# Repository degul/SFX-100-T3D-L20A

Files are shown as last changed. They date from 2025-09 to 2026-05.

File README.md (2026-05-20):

# SimFeedback-T3D-L20A
SFX-100 AC Servo Motor 80AST-A1C02430

카카오톡 오픈 톡방 - https://open.kakao.com/o/gSO9CL0h

3d view - https://a360.co/4tRbJ65

## Servo Motor wiring diagram

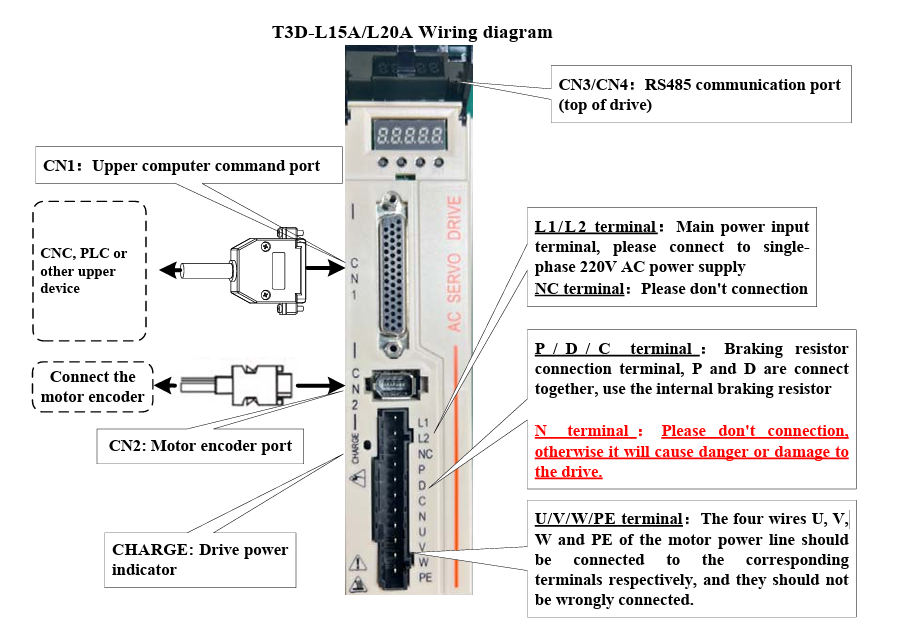
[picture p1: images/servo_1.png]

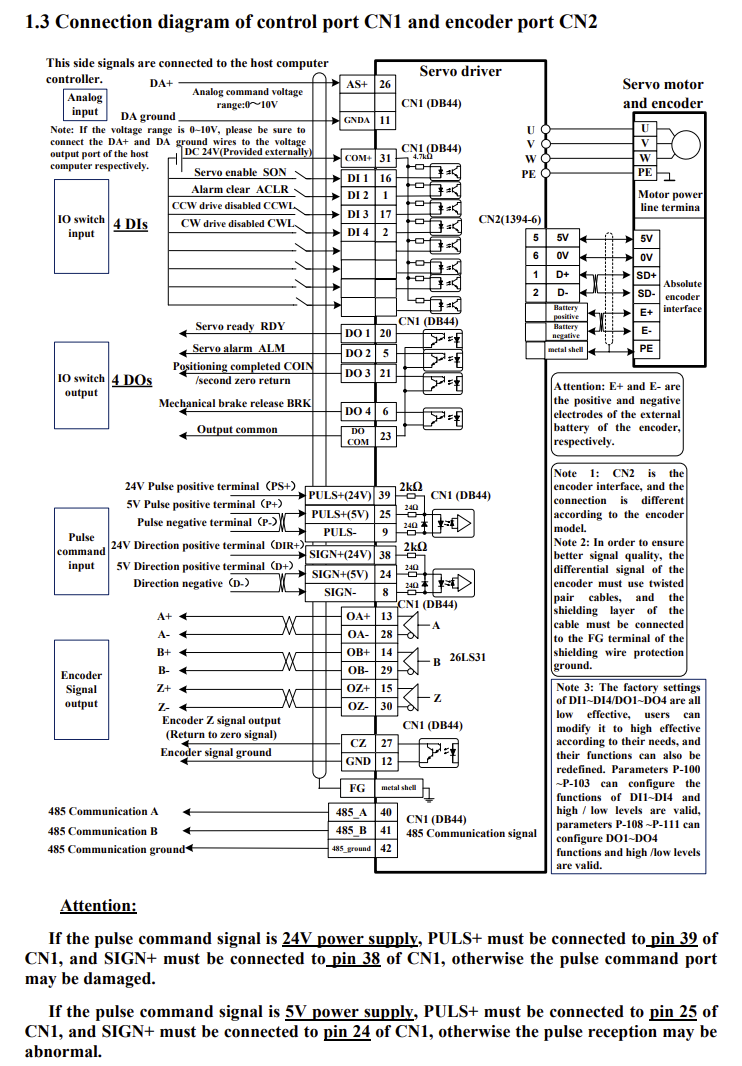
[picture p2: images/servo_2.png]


` L1 / L2 = main power input terminal 220v  `<br>
` U / V / W / PE = motor power cable  `<br>

## SimFeedback + Servo 80AST Pins

### 아두이노 핀 정보

| Pin | Motor 1 | Motor 2 | Motor 3 | Motor 4 | DB25 PIN |
|---|---|---|---|---|---|
| STEP  | 8 | 9 | 10 | 11 | 3 |
| DIR | 4 | 5 | 6 | 7 | 4 |
| ENA | A0 | A1 | A2 | A3 | 6 |
| 5V | 5V | 5V | 5V | 5V | 9 |
| GND | GND | GND | GND | GND | 5, 10, 14 |

### DB25 터미널에 모터드라이브 배선 연결 정보

| DB25 Pin | Label |
|---|---|
| 3 | **P+** |
| 4 | **D+** |
| 6 | **SON** |
| 9 | **24V** |
| 5,10,14  | **P- / D- / 0V** |
---

## 모터드라이브 파라미터

` P-006 ; 25 `<br>
` P-007 ; 30 `<br>
` P-019 ; 60 `<br>
` P-021 ; 20 `<br>
` P-029 ; 16 = 100mm stroke limit `<br>
` P-040 ; 30 `<br>
` P-098 ; 1 (Force Enable)`<br>

### $\color{red}{\textbf{E-set -> done}}$  (값 설정후 저장 및 재시작)
---

<br>
<br>

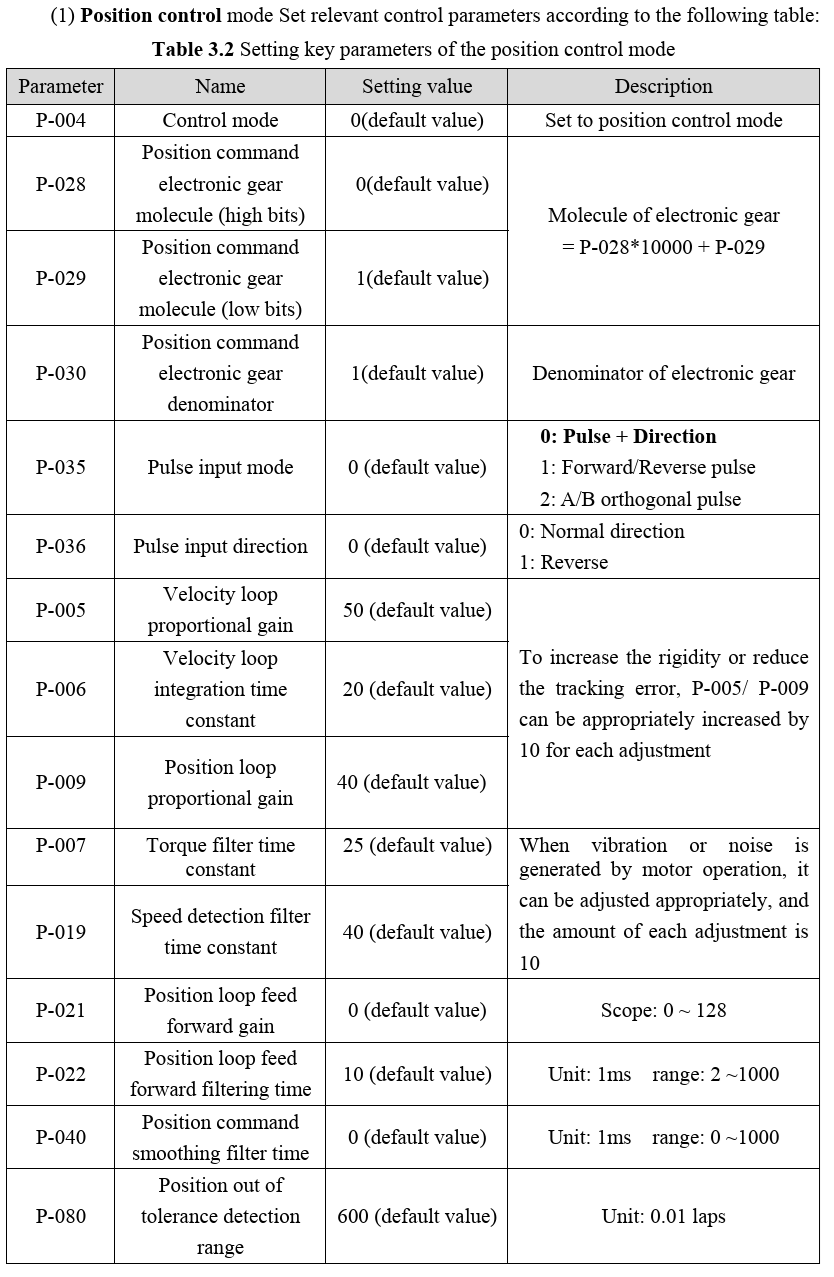
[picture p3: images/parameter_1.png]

<!-- <img src="https://github.com/degul/SimFeedback-T3D-L20A/raw/main/images/parameter_2.png" alt="" width="600"> -->

## SFX-100 

3d view - https://a360.co/4tRbJ65

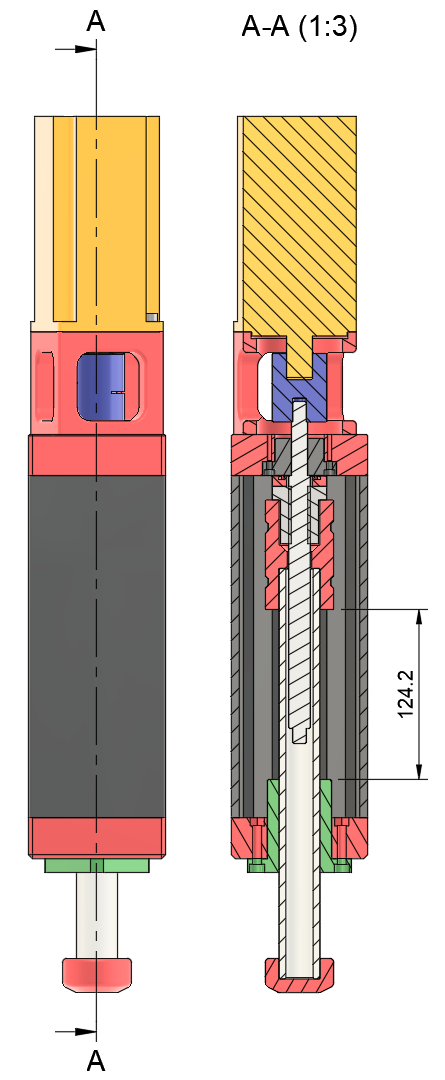
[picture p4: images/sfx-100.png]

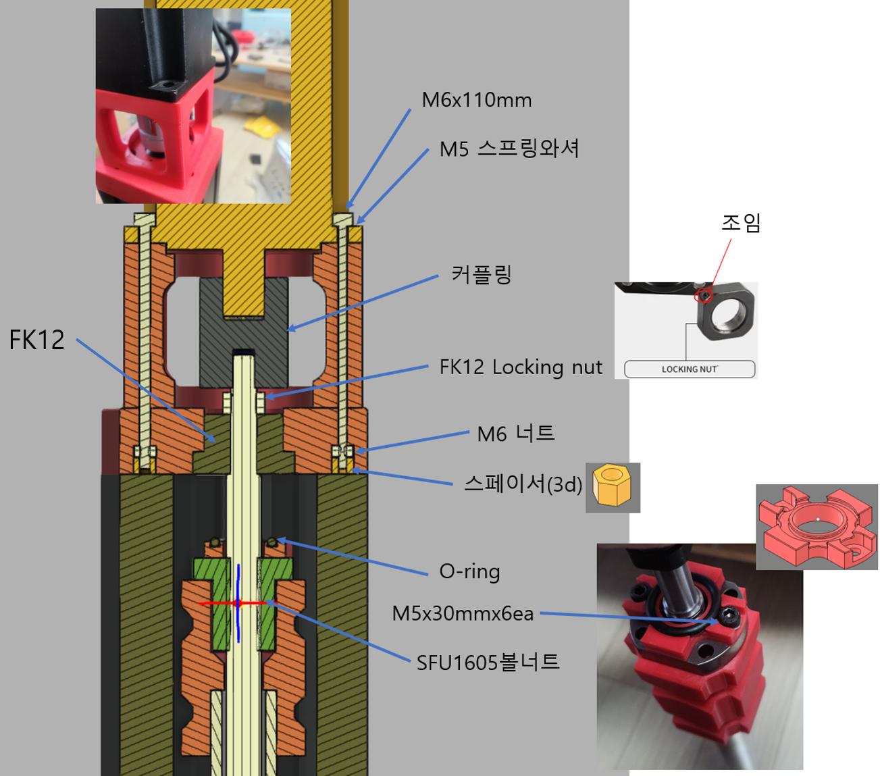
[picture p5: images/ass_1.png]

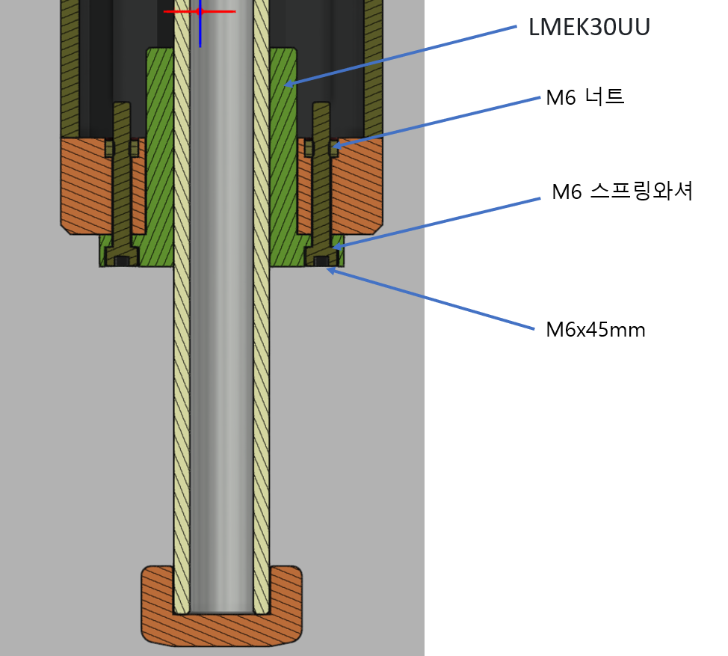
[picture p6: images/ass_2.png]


## Assembly parts

| Part | Type | EA | Link | 
| --- | --- | --- | --- |
| Servo Motor | HLTNC T3D-L20A-RABN 750W 2.4N | 4 | https://www.aliexpress.com/item/1005004869497167.html |
| Coupling | 40X50-10X19 | 4 | https://www.aliexpress.com/item/33014472676.html |
| Rubber Ring | OD30mm CS4mm | 1 (50pcs) | https://www.aliexpress.com/item/1005008292700053.html |
| FK12 |  | 4 | https://www.aliexpress.com/item/32717973925.html |
| SFU 1605 | 250mm, SFU1605(metal nut, 메탈너트선택 꼭)| 4 | https://www.aliexpress.com/item/32813817954.html |
| Hollow Shaft | OD30mm, ID20mm, 300mm | 4 | https://www.aliexpress.com/item/1005003847058846.html |
| LMEK30UU |  | 4 | https://www.aliexpress.com/item/1005003773456962.html |
| Profile 100x100 | $\color{#1e3cb0}{\textbf{조립해서 보내줌}}$ | 1 (4개 포함) | https://www.aliexpress.com/item/1005002770599016.html |
| Grub Screws M8 | $\color{#1e3cb0}{\textbf{조립해서 보내줌}}$ | 1 (32개 포함) | https://www.aliexpress.com/item/1005002797059381.html | 
| EMI Filter | CW4L2-20A | 1 | https://www.aliexpress.com/item/1005004599192534.html | 
| Fast Wire Connector | D1-4O 5PCS | 1 | https://www.aliexpress.com/item/1005007008409625.html | 
| Corner Aluminum Connector  | 4040F | 16 | https://www.aliexpress.com/item/1005007188219353.html | 
| T Block Square Nut M8 | 4040-M8 | 16 | https://www.aliexpress.com/item/1005008879758577.html | 
| T Block Square Nut M8 | 4545-M8 | 16 | https://www.aliexpress.com/item/1005008879758577.html | 
| Arduino Leonardo | | 1 | (아두이노 구매시 아두이노용 USB케이블(파란색) 함께 구매) |
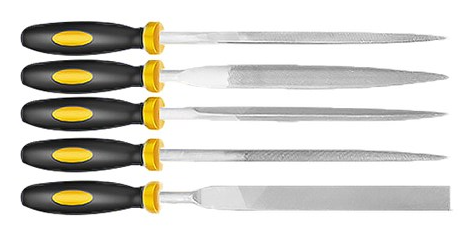
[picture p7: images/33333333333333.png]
| 연마줄 | |   | https://www.coupang.com/vp/products/9031884060 |
| 마스킹테이프 | | | https://www.coupang.com/vp/products/8511069704 |
---

| 육각렌치볼트 | 길이 | 수량 |
| --- | --- | --- |
| DIN912 M8 | 50mm | 32 |
| DIN912 M6 | 110mm | 16 |
| DIN912 M6 | 45mm | 16 |
| DIN912 M5 | 30mm | 24 |
| DIN912 M4 | 25mm | 16 |
---

| 너트 | 수량 |
| --- | --- |
| DIN934 M6 | 32 |
---

| 스프링 와셔 | 수량 |
| --- | --- |
| M8 | 32 |
| M6 | 16 |
| M5 | 40 |
| M4 | 16 | 
---

## SFX-100-Breakout-Board
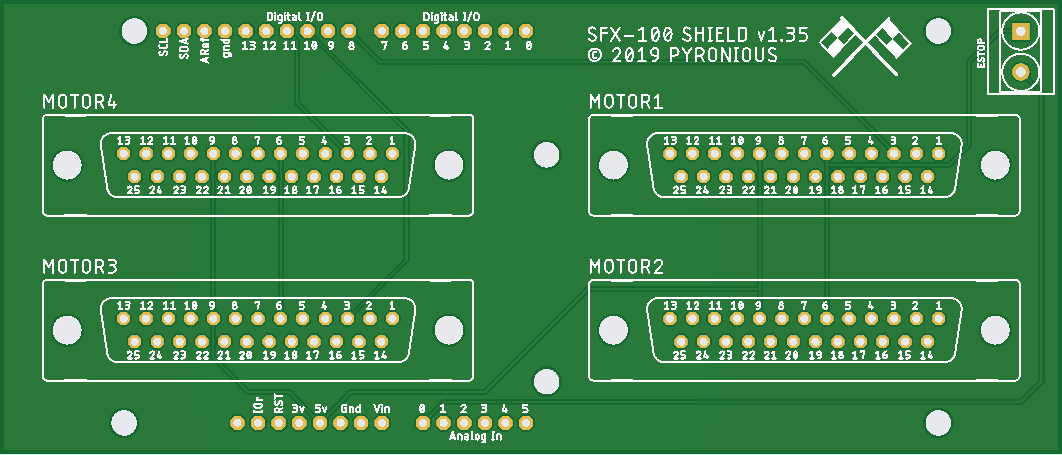
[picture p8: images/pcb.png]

<br>

| Part | Type | EA | Link | 
| --- | --- | --- | --- |
| PCB | PCB Gerber Files - https://github.com/Pyronious/SFX-100-Breakout-Board/tree/master/Group%20Buy%20Edition/Gerber%20Files | | https://jlcpcb.com/ |
| DB25 | $\color{red}{\textbf{Female}}$ | 4 | https://www.aliexpress.com/item/1005006034780514.html |
| DB25 Terminal | $\color{red}{\textbf{Male Nut}}$ | 4 | https://www.aliexpress.com/item/32878748465.html |
| KF301 | 2P (비상버튼 사용할때 필요) | 1 | https://www.aliexpress.com/item/1005005695451188.html |
---

3D Model of Case
https://github.com/Pyronious/SFX-100-Breakout-Board/tree/master/Group%20Buy%20Edition/Enclosure

## 3D 프린팅 부품
| Part | EA | |
| --- | --- | --- |
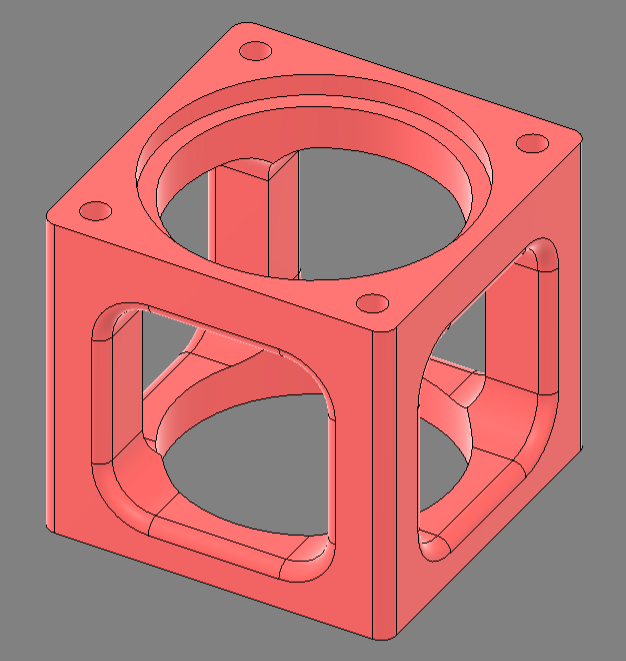
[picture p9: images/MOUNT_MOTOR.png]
| MOUNT_MOTOR | 4 |  | 
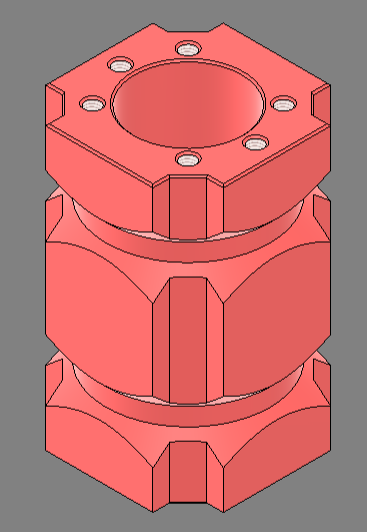
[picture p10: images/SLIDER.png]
| SLIDER | 4 |  |
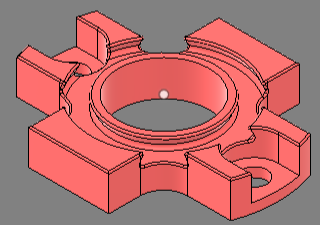
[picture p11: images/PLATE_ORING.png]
| PLATE_ORING | 4 |  |
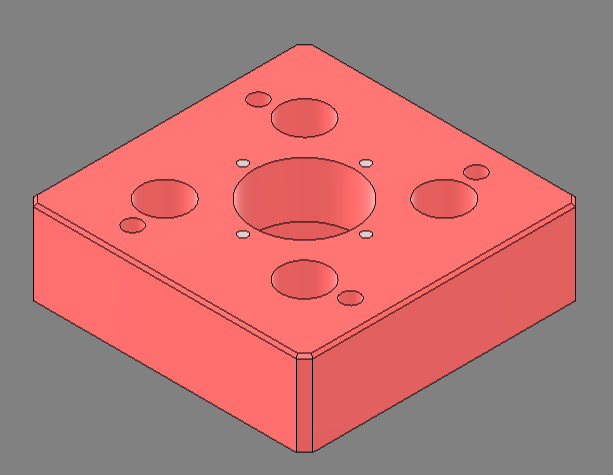
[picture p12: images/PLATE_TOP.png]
| PLATE_TOP | 4 |  |
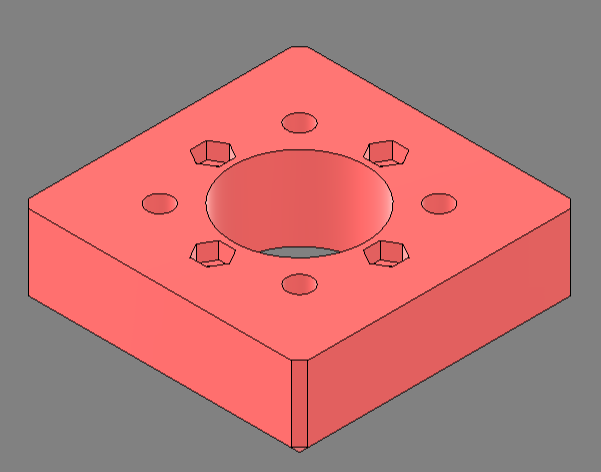
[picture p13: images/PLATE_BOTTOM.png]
| PLATE_BOTTOM | 4 |  |
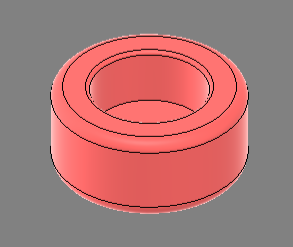
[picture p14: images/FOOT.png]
| FOOT | 4 |  |
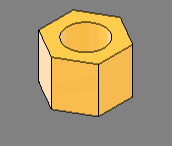
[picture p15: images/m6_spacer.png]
| m6_spacer | 16 |  |

## 3D 프린터 설정 

bump stop / slider 0.4mm 노즐 출력 (정밀성)

0.4mm 노즐 출력 세팅
| 설정 항목 | 권장 값 |  
| --- | --- |
| 노즐 직경 | **0.4mm** | 
| 레이어 높이 | **0.2mm** | 
| Perimeter(외벽 수) | **5개** |  
| 상/하단 레이어 | 8개  |  
| 인필 밀도 | **25%**, Grid 패턴 |  
| 브림 | **5mm** | 

참고 - https://www.xsimulator.net/community/threads/diablo2112s-4-axis-sfx-100-build.13571/page-3#post-185076

## 전원배선(220v)

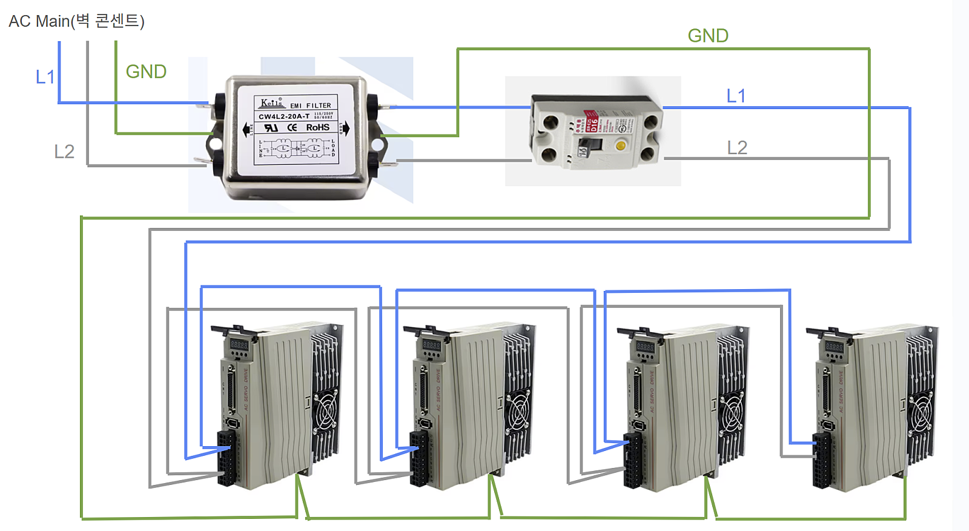
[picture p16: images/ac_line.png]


## Surge

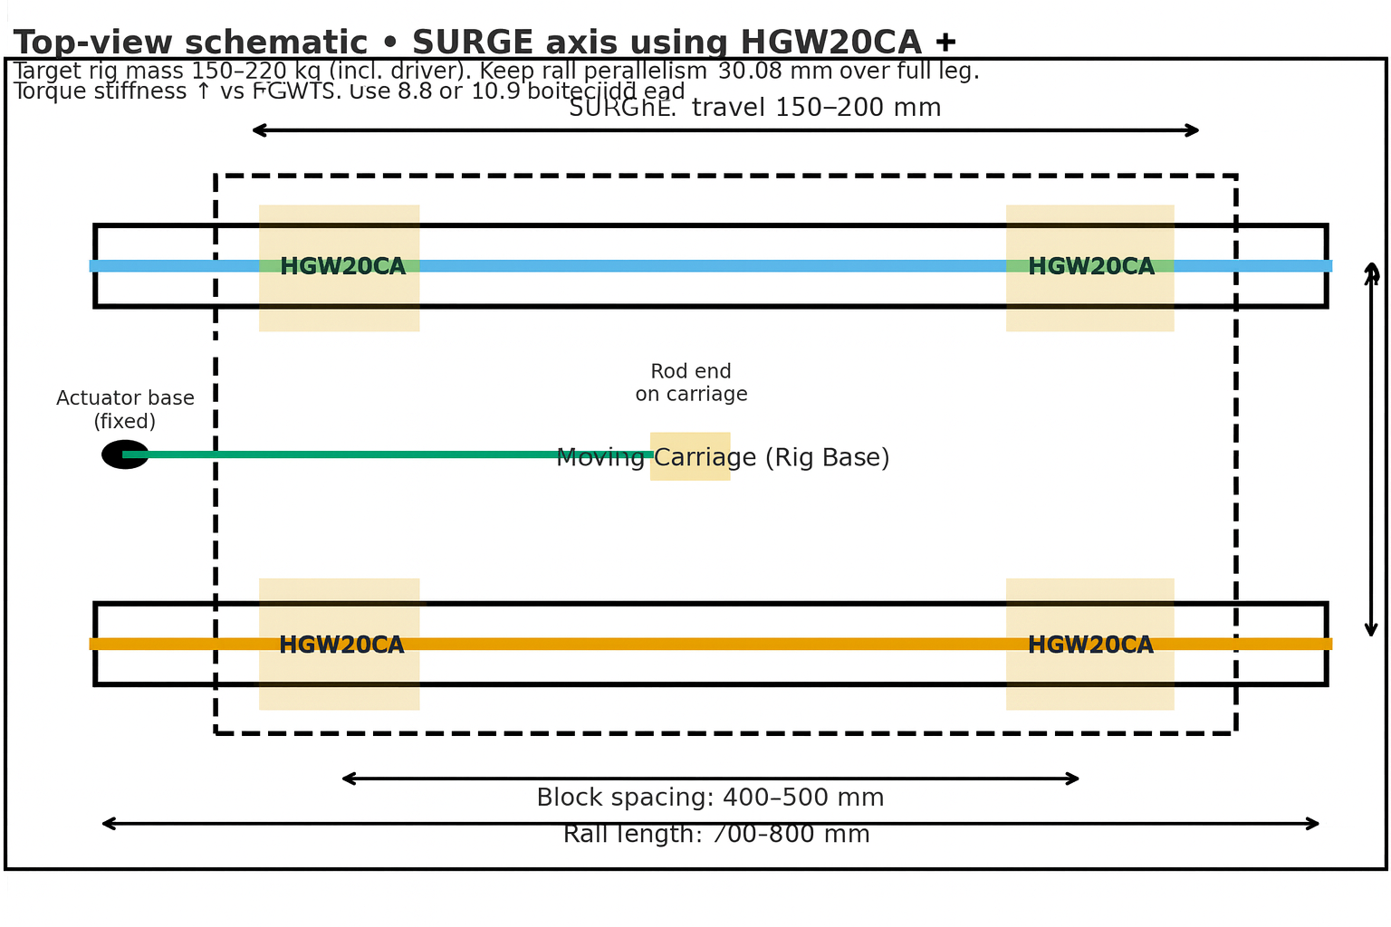
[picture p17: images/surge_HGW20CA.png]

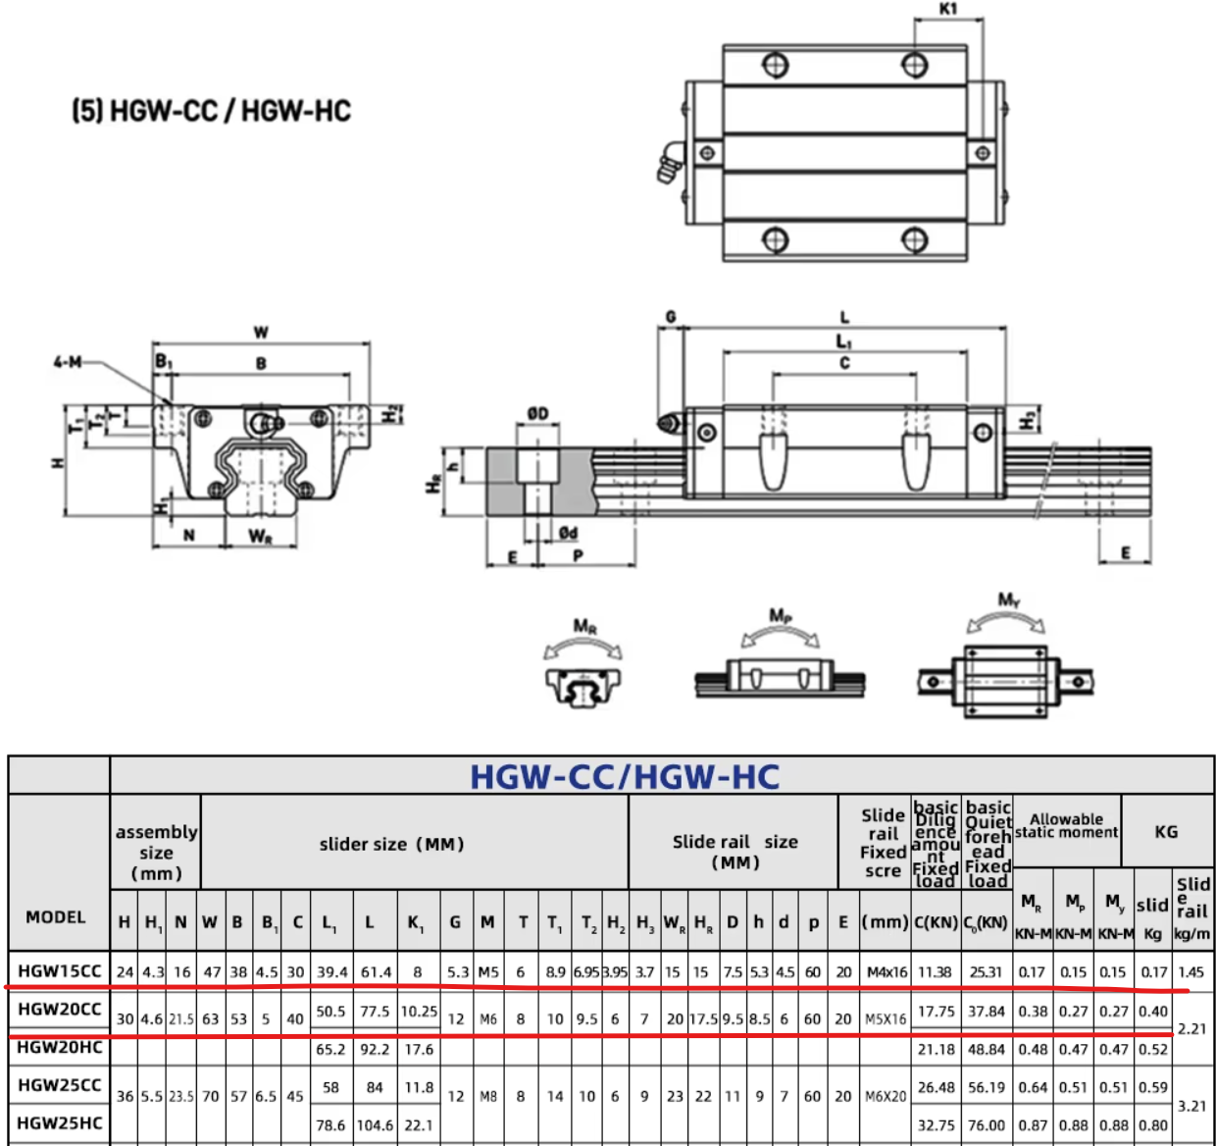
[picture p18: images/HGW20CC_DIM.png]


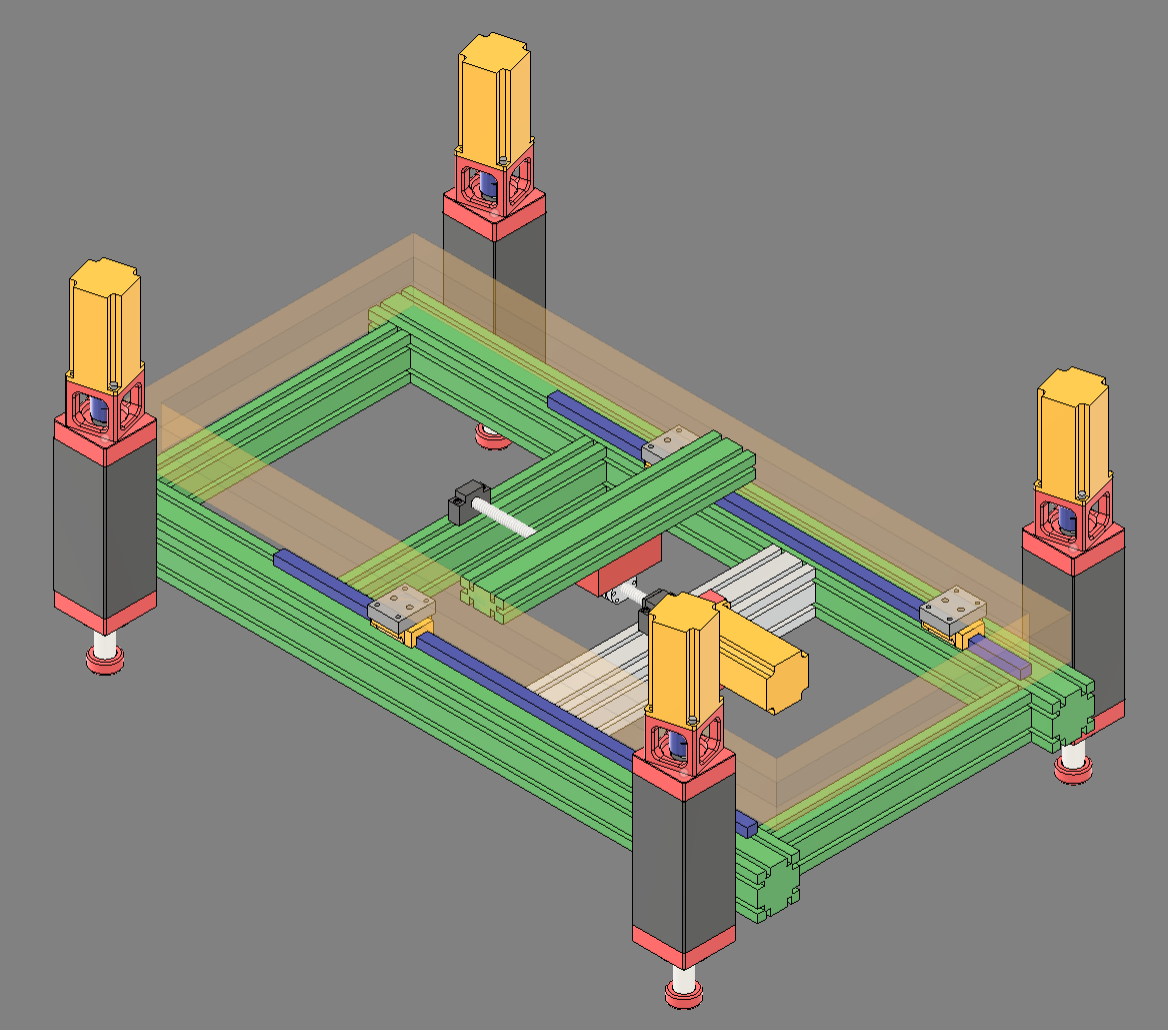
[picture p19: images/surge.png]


-----------------------------------------

<!-- 
## monitor

<img src="https://github.com/degul/SimFeedback-T3D-L20A/raw/main/images/monitor_cockpit.png" alt="">

-->

## 다운로드

https://raw.githubusercontent.com/degul/SFX-100-T3D-L20A/main/ext/Simfeedback_flash.zip    (firmware flash)
https://raw.githubusercontent.com/degul/SFX-100-T3D-L20A/main/ext/SRT80.leonardo.zip    (SRT80일때는 P29-3 = 100mm 매우중요!)

## 참고 링크

https://opensfx.com/

https://github.com/SimFeedback/SimFeedback-AC-Servo

https://github.com/SHWotever/SimHubMotionPresets

https://opensfx.com/2019/04/09/sfx-100-shield/

https://github.com/Pyronious/SFX-100-Breakout-Board/tree/master/Group%20Buy%20Edition/Gerber%20Files

https://forum.virtualracing.org/threads/3dof-motion-fuer-1000eur-bauen-geht-das.144073/

## 참고 문서

https://cnc-tehnologi.ru/files/t3d_servo_ENpdf.pdf

https://www.hlt-cnc.com/uploads/38006/files/T3D-Full-manual-V2.3_-English-version.pdf

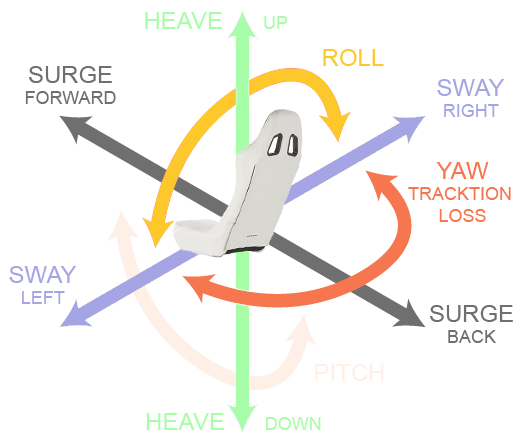
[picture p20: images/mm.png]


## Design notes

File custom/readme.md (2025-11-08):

## Parameters

` P-006 ; 25 `<br>
` P-007 ; 30 `<br>
` P-019 ; 60 `<br>
` P-021 ; 20 `<br>
` P-029 ; 3 = 100mm, 6 = 200mm stroke limit (!important)`<br>
` P-040 ; 30 `<br>
` P-098 ; 1 (Force Enable) (비상버튼 사용시; 0)`<br>

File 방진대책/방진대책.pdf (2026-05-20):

방진 대책.

1. 저가형 Support Block의 Bearing 문제
문제점 : 저가형 Bearing Ball회전 마찰로 인해 마찰된 진동이 프로파일을 타고 바닥으로 전달된다.
해결 : 일제 NSK Bearing 으로 교체 “FK12” 의 Bearing은 6001 베어링이다.

베어링 형번에서 Z,ZZ는 실을 뜻하는것인데, 아무거나 써도 무방하다.

2. Motor의 튜닝 문제
문제점 : 조립에 대한 Motor의 강성 및 출고 시점 모터의 셋팅이 틀림 해결 : 드라이버 튜닝
3. 엑츄에이터에서 전달되는 방진 대책의 문제
문제점 : 모션에 전달되는 진동이 바닥으로 내려오면 바닥을 울린다. 해결 : 에어스프링, 고무패드 조합

## 1. Ball Screw Support Block Bearing 교체 방법

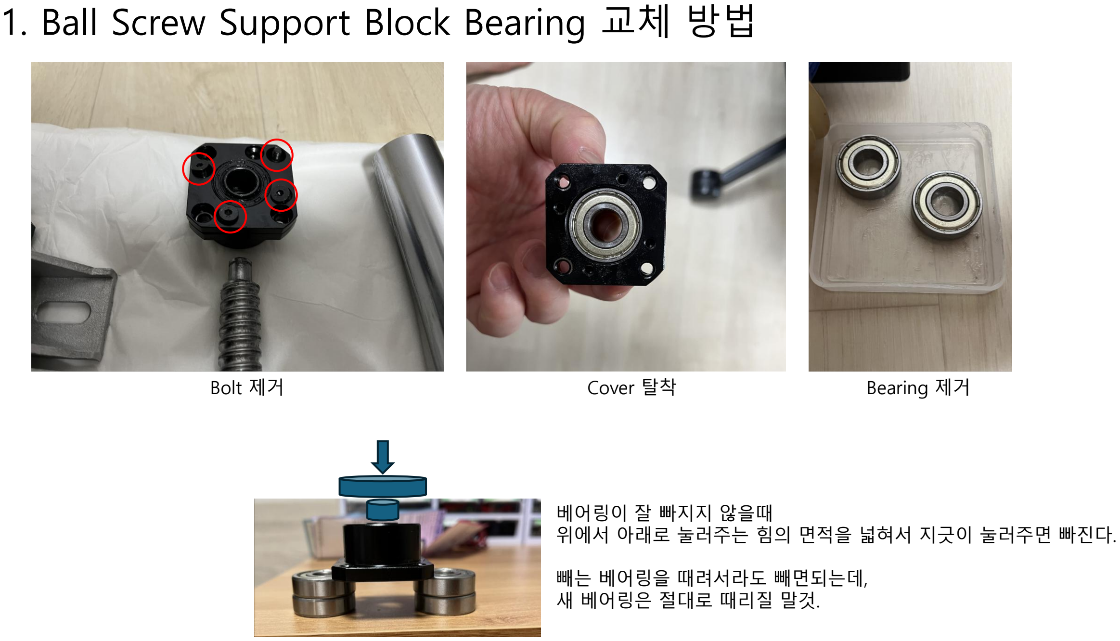
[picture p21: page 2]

Bolt 제거 | Cover 탈착 | Bearing 제거

베어링이 잘 빠지지 않을때
위에서 아래로 눌러주는 힘의 면적을 넓혀서 지긋이 눌러주면 빠진다.

빼는 베어링을 때려서라도 빼면되는데,
새 베어링은 절대로 때리질 말것.

## 2. 방진 대책

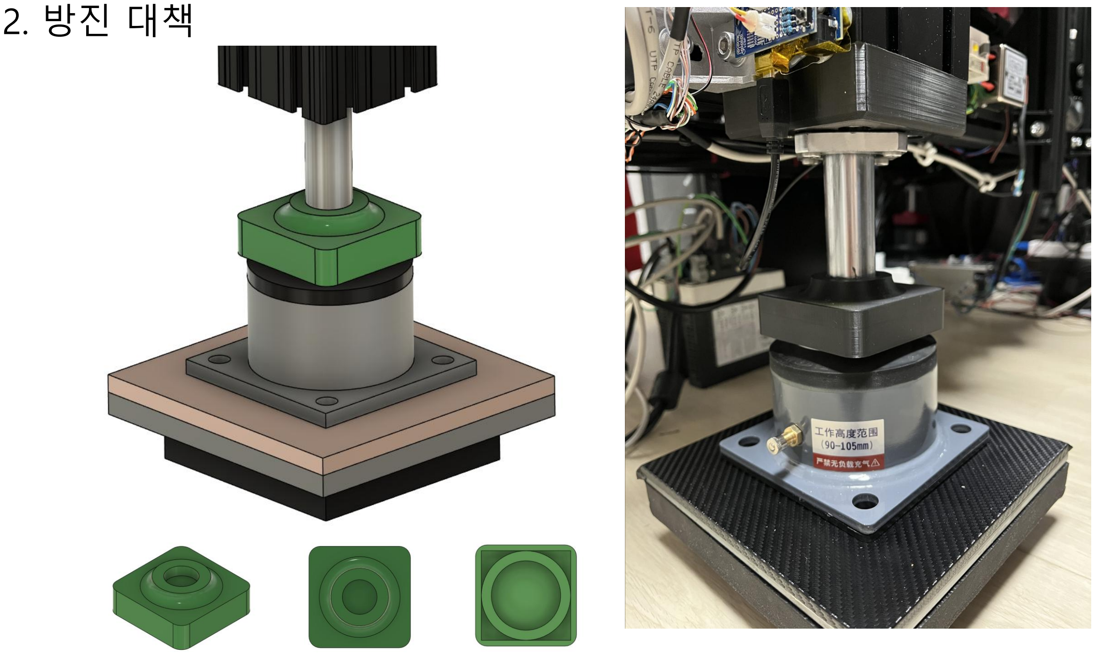
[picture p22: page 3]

## 구매 사이트 (https://item.taobao.com/item.htm?from=detail&id=577328525370)

## 2. 방진 대책

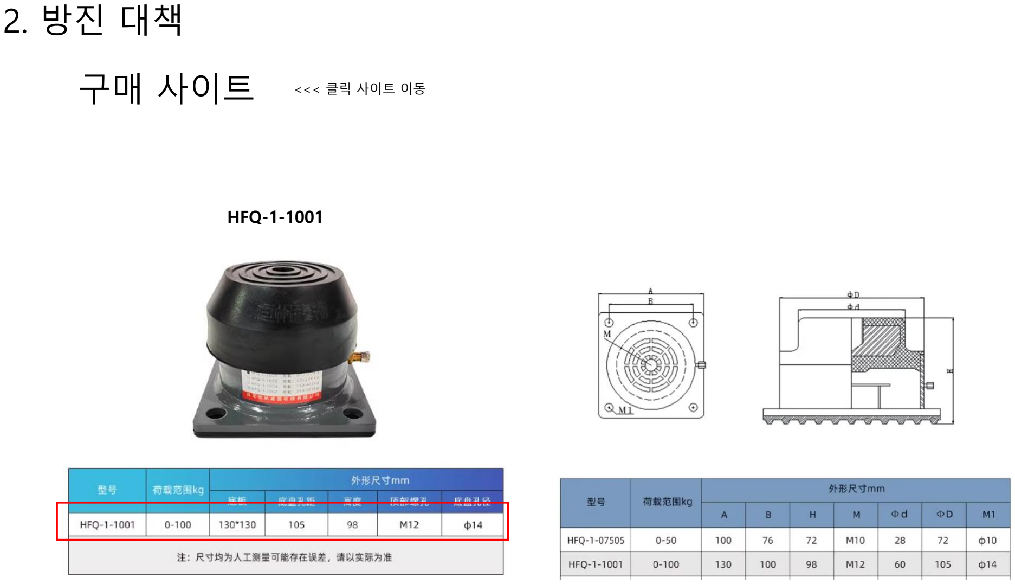
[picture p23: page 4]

<<< 클릭 사이트 이동

구매 사이트

HFQ-1-1001

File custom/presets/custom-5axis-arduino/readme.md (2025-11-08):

Preset compatible with https://lebois-racing.fr/competition-control-box-pour-les-verins-srt80

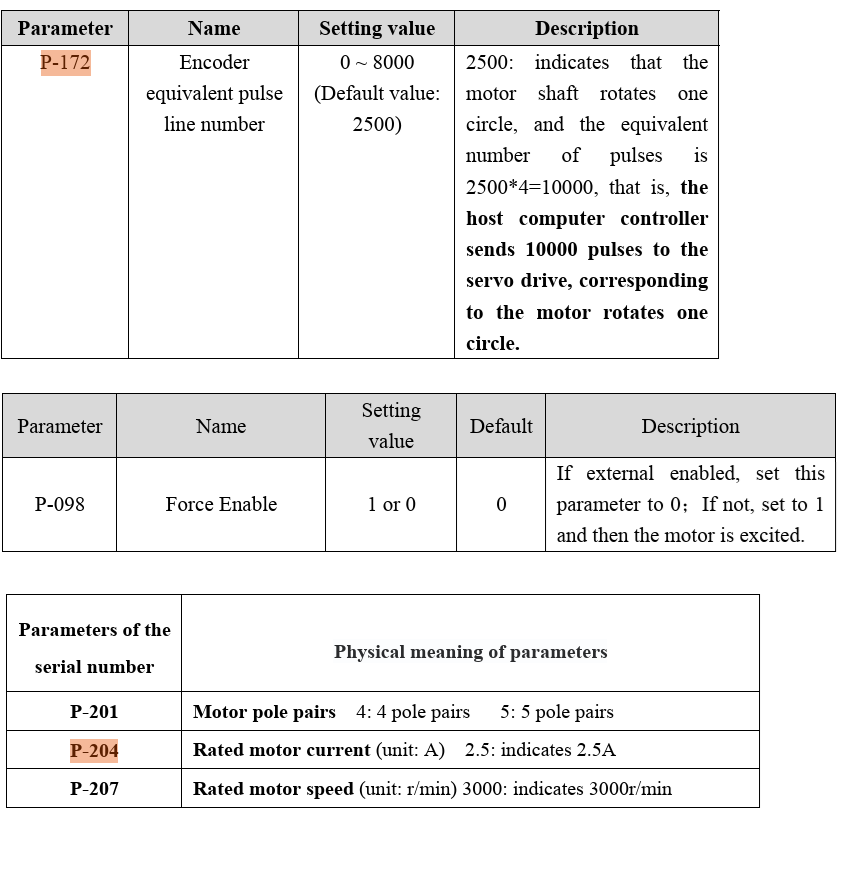
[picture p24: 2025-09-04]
images/parameter_2.png

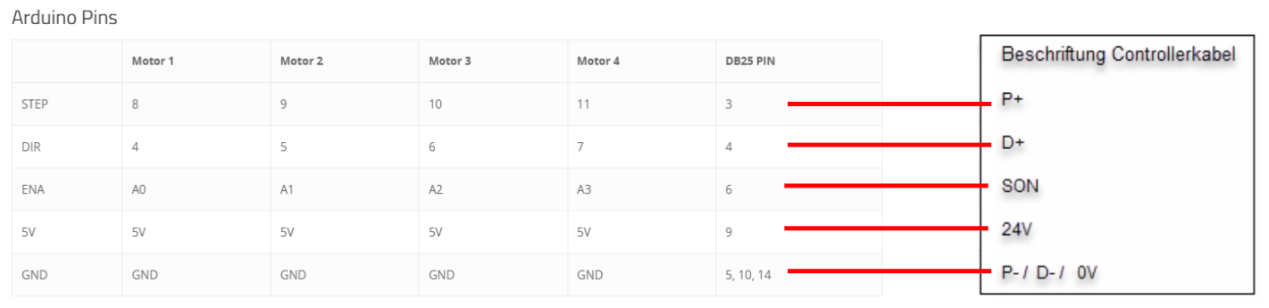
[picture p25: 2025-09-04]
images/pins_1.png

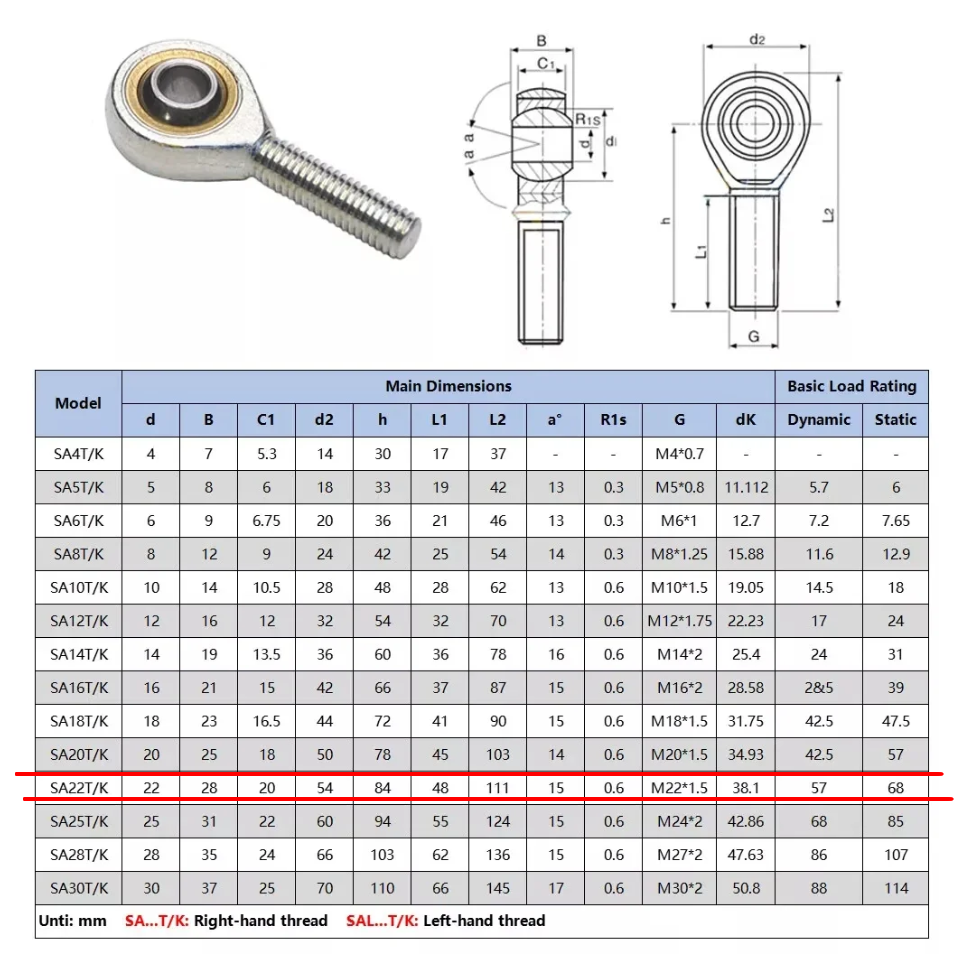
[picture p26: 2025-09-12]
images/SA22.png

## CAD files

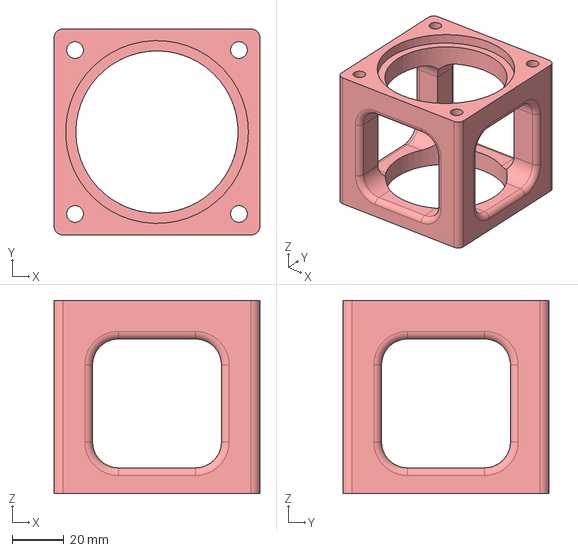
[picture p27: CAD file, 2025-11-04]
3D_Models/MOUNT_MOTOR.step
80.0 x 80.0 x 75.0 mm

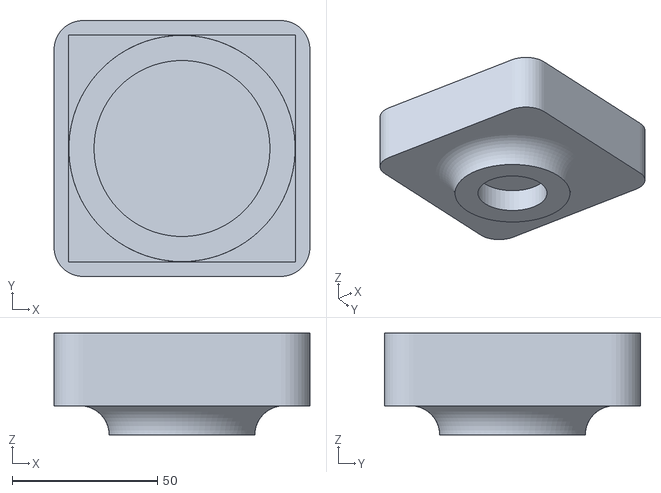
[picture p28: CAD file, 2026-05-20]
방진대책/에어스프링_어댑터2.stl
88.0 x 88.0 x 35.0

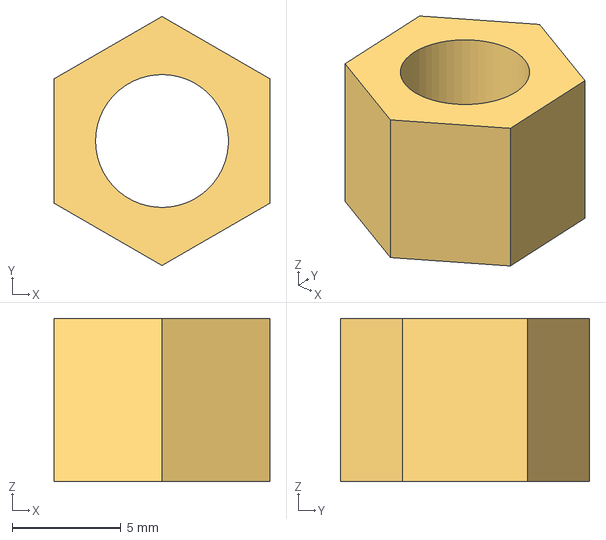
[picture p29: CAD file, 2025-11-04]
3D_Models/m6_spacer.step
9.90 x 11.4 x 7.50 mm

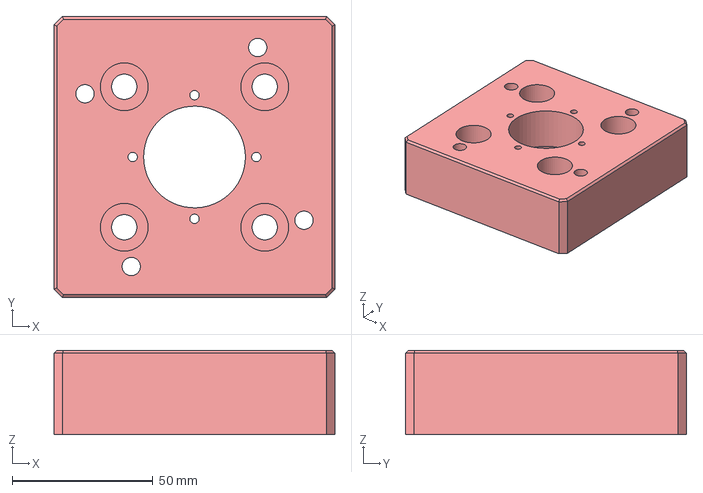
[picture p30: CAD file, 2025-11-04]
3D_Models/PLATE_TOP.step
100.0 x 100.0 x 30.0 mm

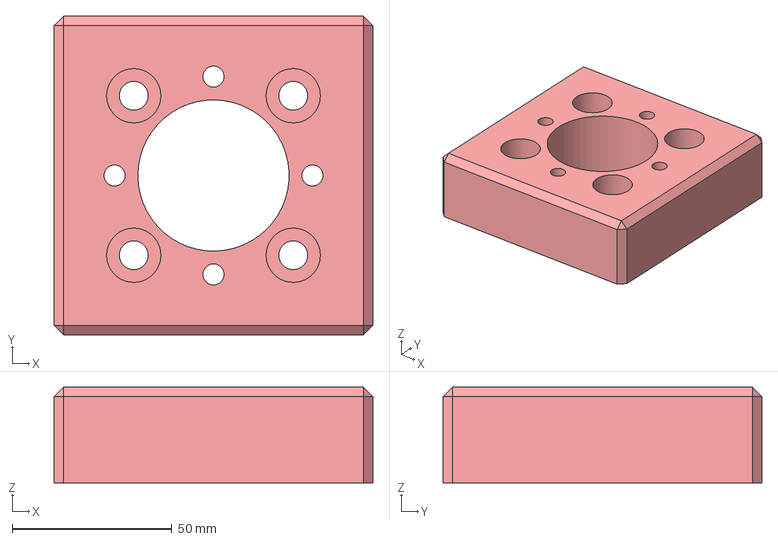
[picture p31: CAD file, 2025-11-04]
3D_Models/PLATE_BOTTOM.step
100.0 x 100.0 x 30.0 mm

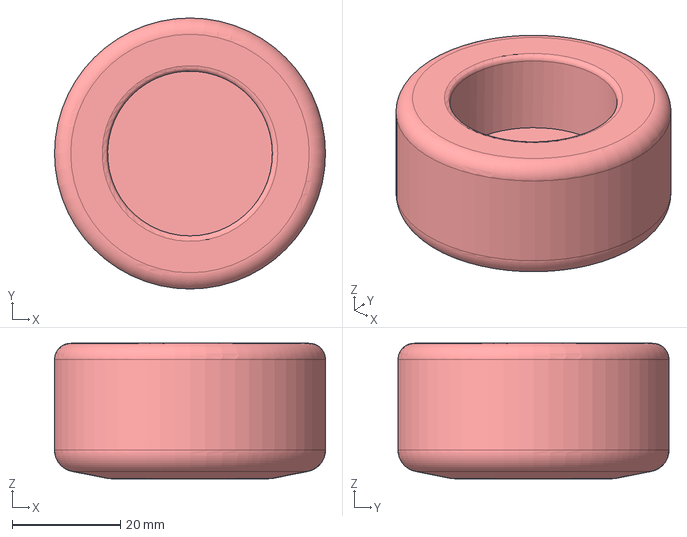
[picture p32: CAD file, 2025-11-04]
3D_Models/FOOT.step
50.0 x 50.0 x 25.0 mm

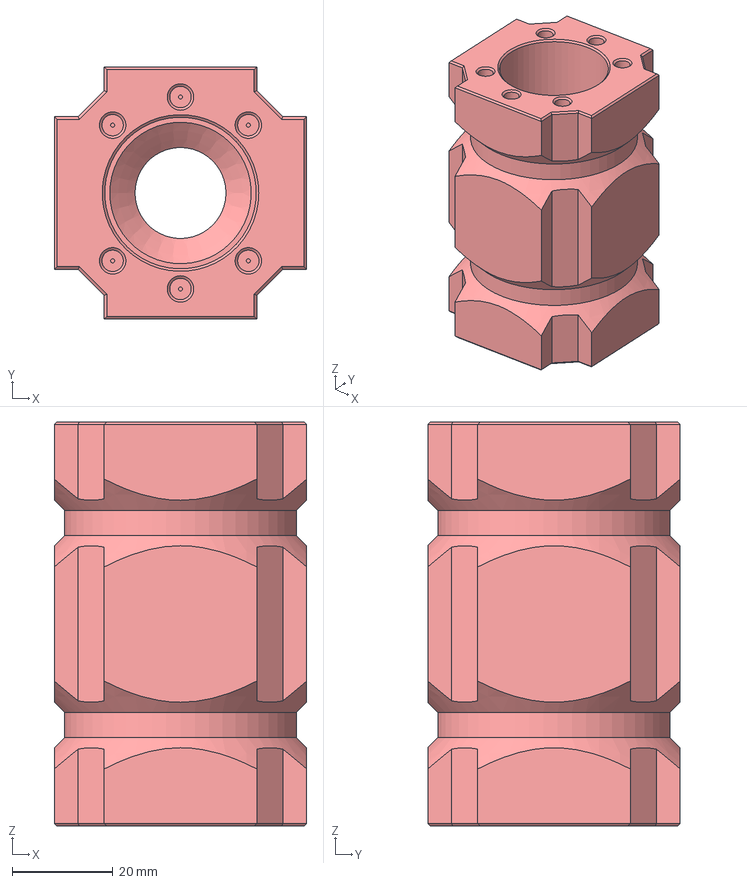
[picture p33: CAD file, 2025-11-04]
3D_Models/SLIDER.step
50.0 x 50.0 x 80.0 mm

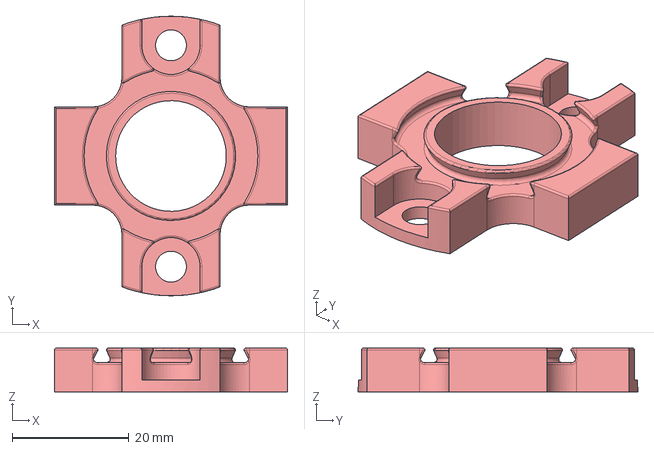
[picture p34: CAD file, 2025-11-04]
3D_Models/PLATE_ORING.step
40.0 x 48.0 x 7.50 mm

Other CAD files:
3D_Models/SFX-100.f3z
방진대책/에어스프링_어댑터2.f3d

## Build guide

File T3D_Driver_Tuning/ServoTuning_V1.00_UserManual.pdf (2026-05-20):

# ServoTuning User Manual

(V1.00)

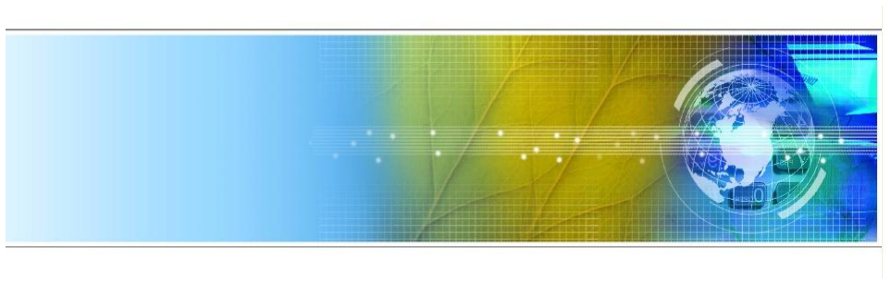
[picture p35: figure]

## September 2025

# Contents

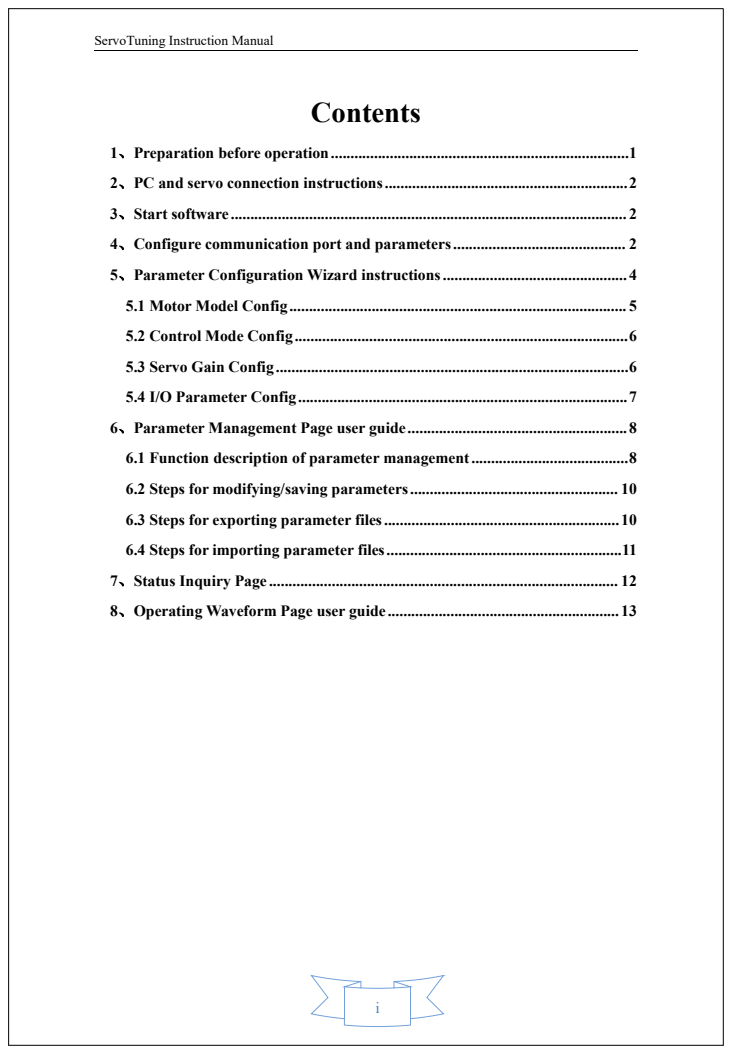
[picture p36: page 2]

ServoTuning Instruction Manual

ServoTuning software is auxiliary debugging software for servo systems in a PC environment, features include a parameter configuration wizard, parameter read/write and save functions, parameter import/export capabilities, status inquiry, and real-time variable oscilloscope monitoring, significantly enhancing debugging efficiency. 1、Preparation before operation

This software is a portable version, Locate file | in
directory file ServoTuning_English and double-click it to run it directly. Windows 7 and later operating systems do not require driver installation;

Windows XP and earlier operating systems require installation of the .NET driver package(users need to download it themselves. If an error occurs during software operation, a prompt will pop up to install the corresponding .NET driver package ). User must supply their own 485-to-USB converter for connecting the servo to

PC. Driver installation depends on converter specification. Attention：Please ensure your servo has RS-485 communication functionality

to work with this software。
Suggested RS485 to USB conversion cable (alternative brands are acceptable):

## 2、PC and servo connection instructions

After completing the above preparations, connect the PC to the servo drive's 485 communication port using the USB/RS485 converter cable as shown in the diagram below:

## 3、Start software

This software is a portable version, Locate file | in
directory file ServoTuning_English and double-click it to run it directly.(Do not modify or delete any other files in this directory, as this may cause software
malfunction).Create a desktop shortcut for the .exe file | to
launch the software directly. Startup interface below:

## 4、Configure communication port and parameters

The data interaction between ServoTuning software and the servo drive is established via the PC's serial port and the drive's RS485 port. Proper configuration of the PC's communication port and servo drive communication parameters (P-181/P-182/P-183) is required. Users must correctly configure the PC's communication port and servo communication parameters according to the following steps ①②③④:

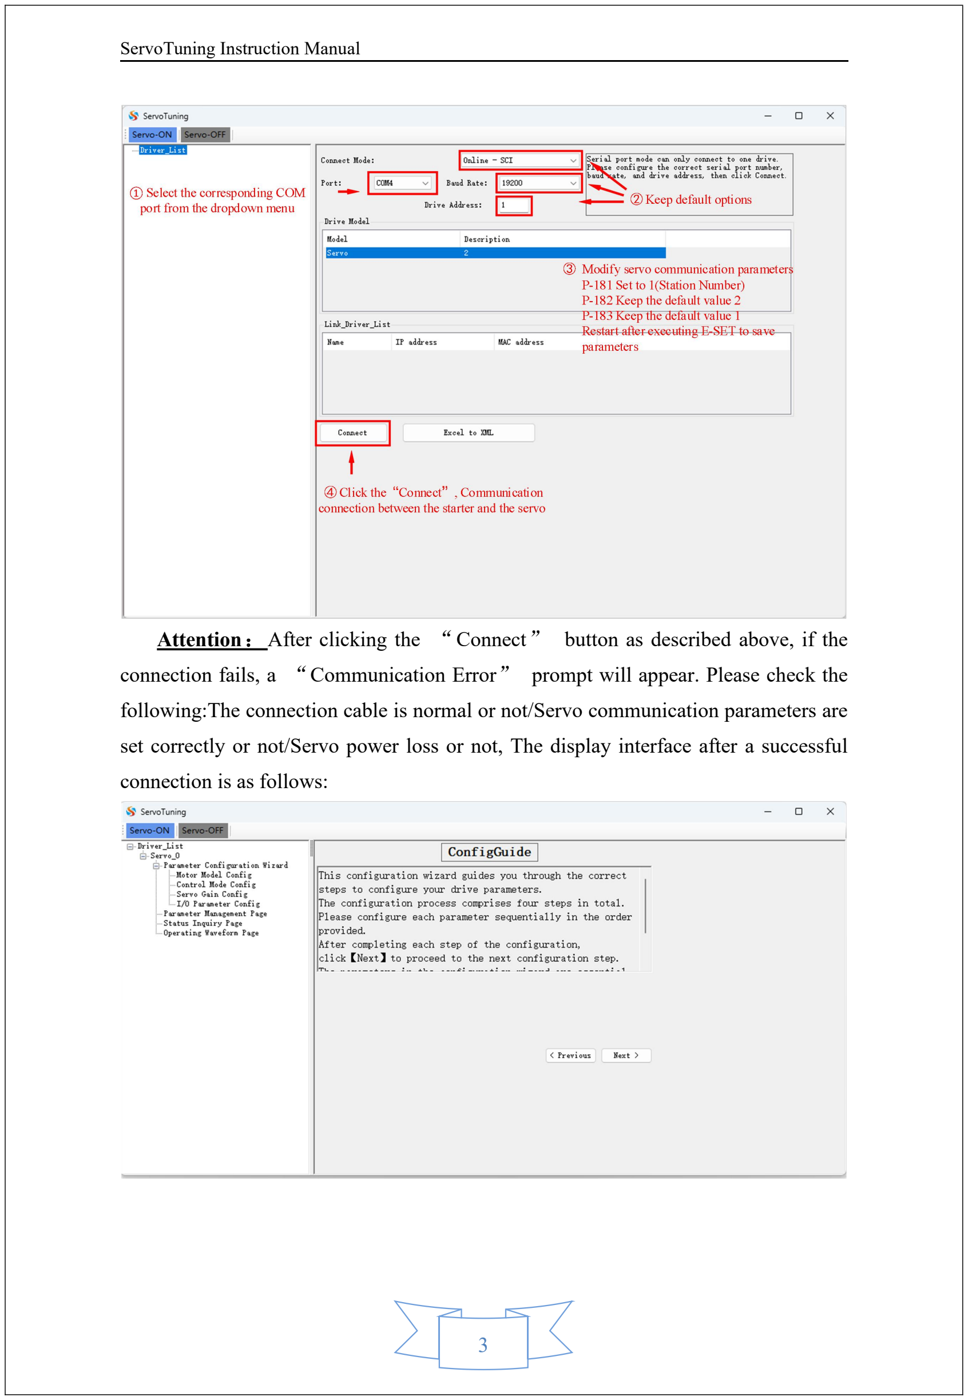
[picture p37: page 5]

Attention：After clicking the “Connect” button as described above, if the connection fails, a “Communication Error” prompt will appear. Please check the following:The connection cable is normal or not/Servo communication parameters are set correctly or not/Servo power loss or not, The display interface after a successful connection is as follows:

## 5、Parameter Configuration Wizard instructions

Parameter Configuration Wizard guides users through the correct steps to configure common parameters for servo. It is divided into four subpages: Motor Model Config (motor model parameter configuration), Control Mode Config (control mode parameter configuration), Servo Gain Config (servo gain parameter configuration), and I/O Parameter Config (Input/Output Parameter Function Configuration. The parameter configuration steps are as follows:
① On the Motor Model Config page，Set Motor Series (P-099) and Motor Code (P-002), then perform the E-DEF operation (this step must be performed), restore the motor's default control parameters. ② On the Control Mode Config page, set the Control mode (P-004) and the basic

parameters for the corresponding mode according to actual requirements. ③ On the Servo Gain Config page, adjust the stiffness and filter parameters as

needed based on the actual performance. ④ On the I/O Parameter Config page, configure the functional parameters for DI

/ DO according to actual requirements. After completing the above parameter settings, then perform the E-SET

operation, the set parameters will be saved to the memory chip.The Configuration Wizard page lists only the essential parameters required for normal operation of the servo. Configuration of other parameters must be performed on the “Parameter Management Page.” The interface of the parameter configuration wizard is displayed as follows:

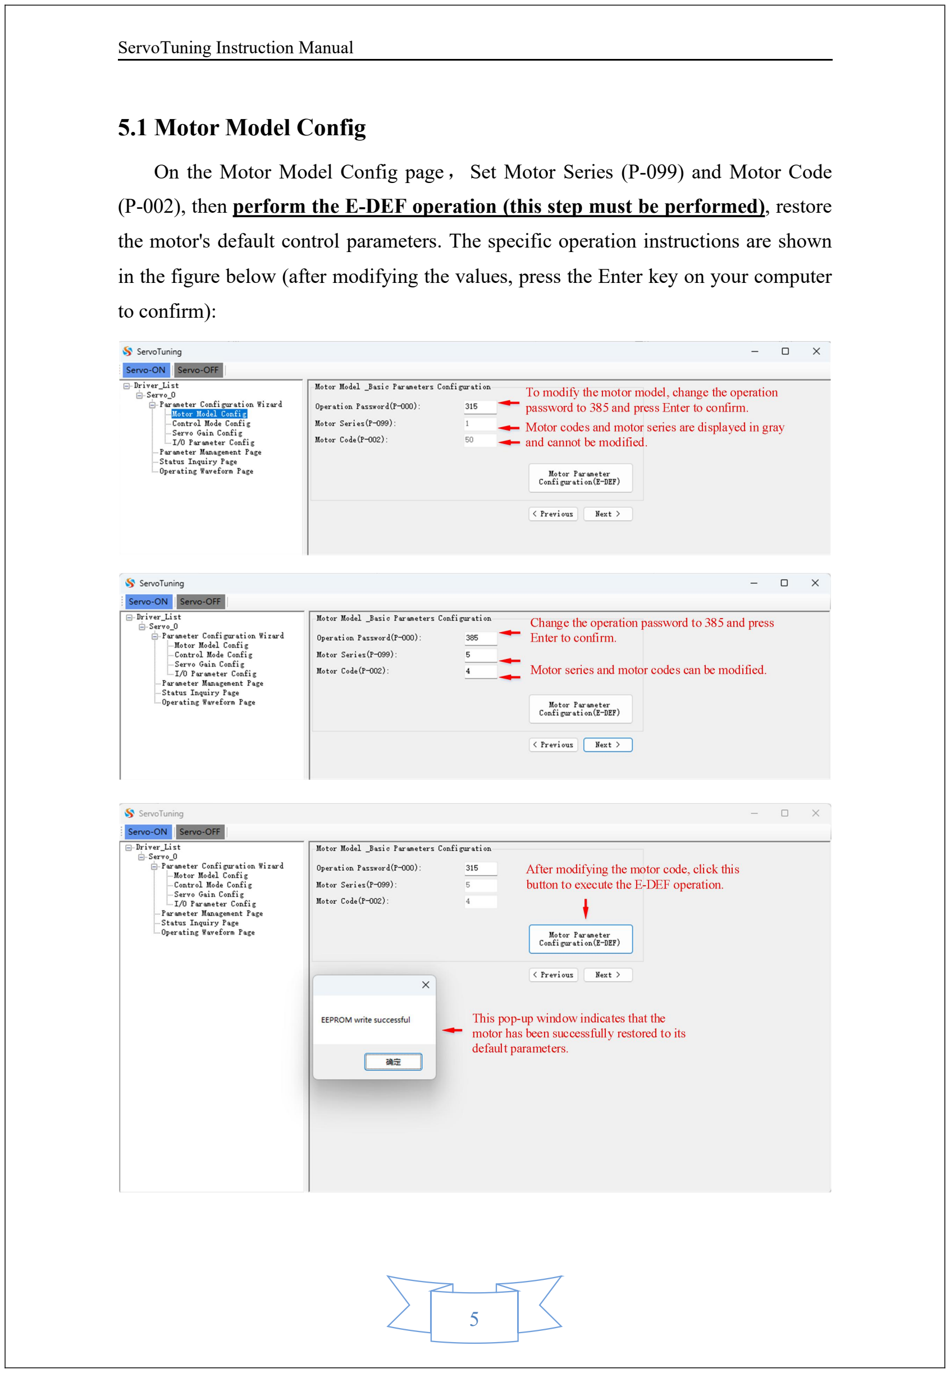
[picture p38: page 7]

### 5.1 Motor Model Config

On the Motor Model Config page，Set Motor Series (P-099) and Motor Code (P-002), then perform the E-DEF operation (this step must be performed), restore the motor's default control parameters. The specific operation instructions are shown in the figure below (after modifying the values, press the Enter key on your computer to confirm):

### 5.2 Control Mode Config

After completing the motor model configuration and E-DEF operation, click “Next” to enter the Control Mode Config page. On this page, you can set the servo's control mode (P-004) and related parameters for position mode, speed mode, and torque mode. Specific operation instructions are shown in the figure below (press Enter to confirm after modifying values):

### 5.3 Servo Gain Config

On the Servo Gain Config page, you can adjust the stiffness and filter parameters as needed based on the actual performance. The specific operation instructions are shown in the figure below (press Enter to confirm after modifying values):

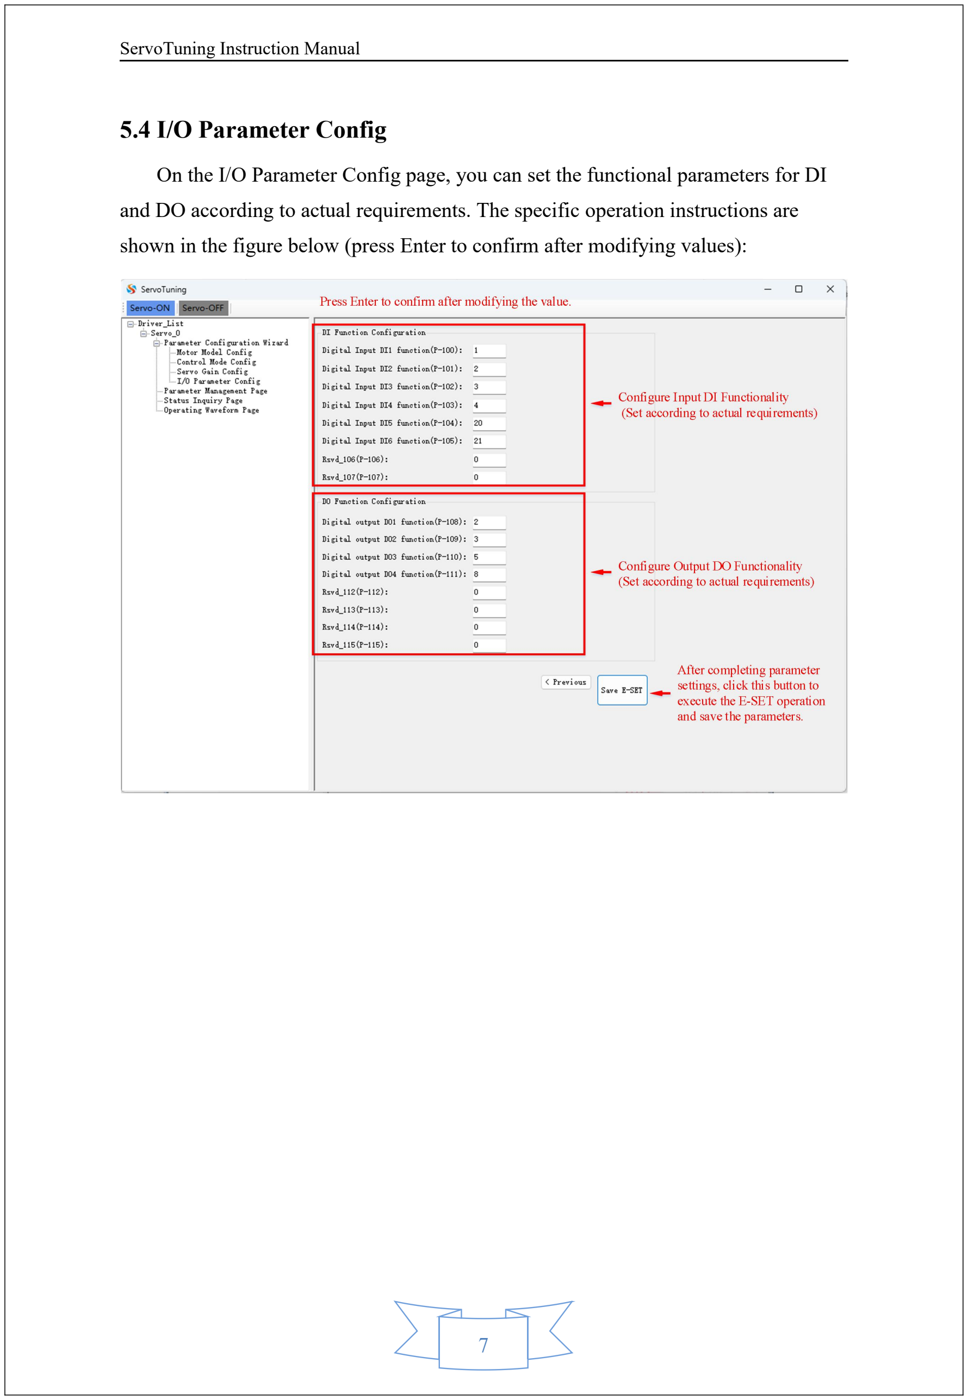
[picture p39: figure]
5.4 I/O Parameter Config

On the I/O Parameter Config page, you can set the functional parameters for DI and DO according to actual requirements. The specific operation instructions are shown in the figure below (press Enter to confirm after modifying values):

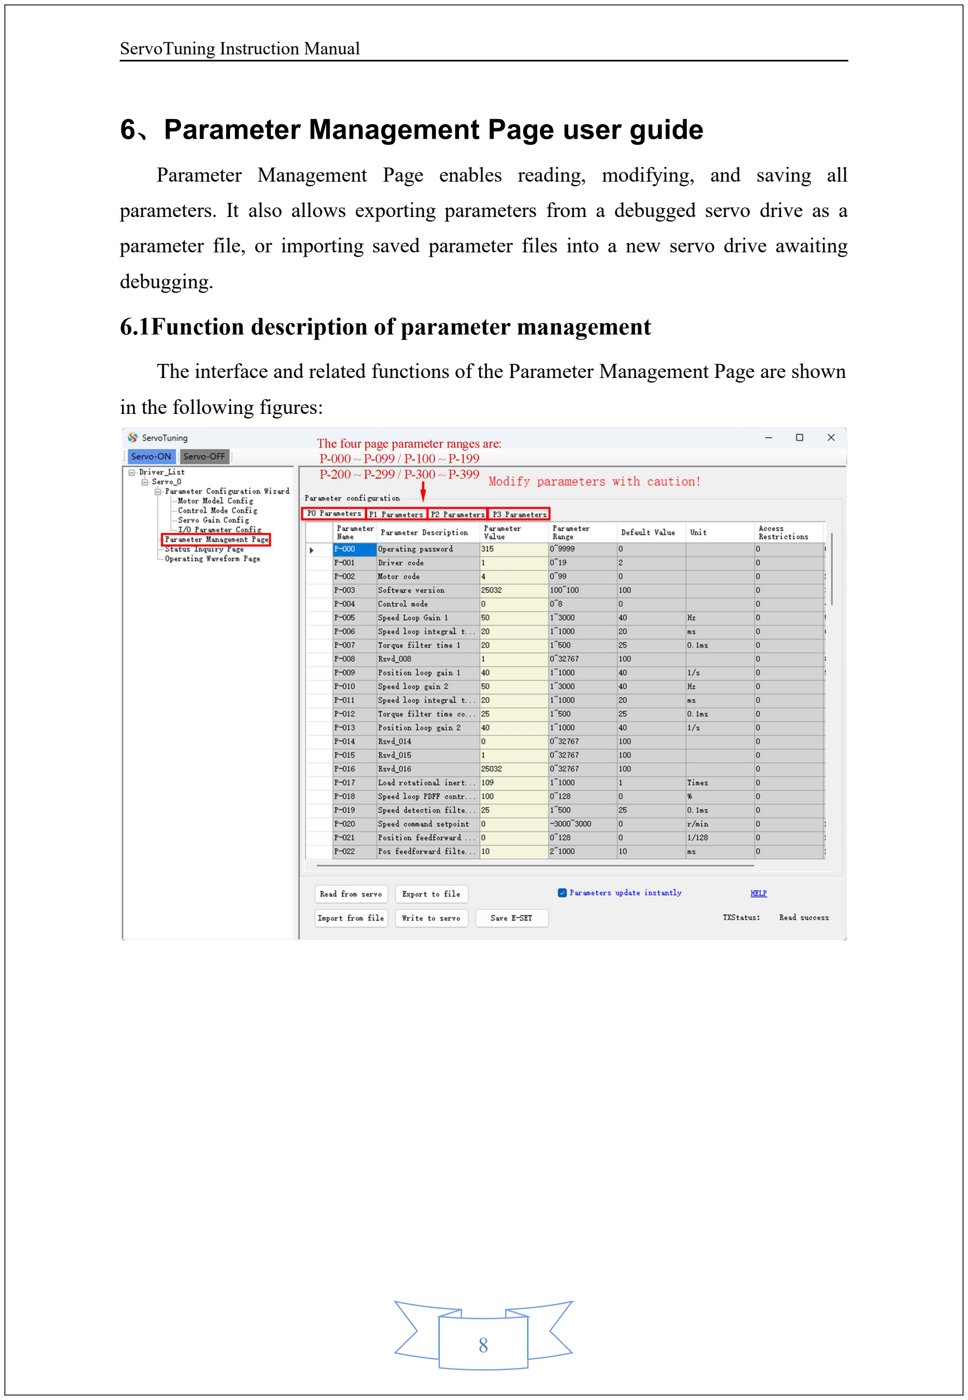
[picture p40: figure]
6、Parameter Management Page user guide; in the following figures:

Parameter Management Page enables reading, modifying, and saving all parameters. It also allows exporting parameters from a debugged servo drive as a parameter file, or importing saved parameter files into a new servo drive awaiting

### debugging. 6.1Function description of parameter management

The interface and related functions of the Parameter Management Page are shown

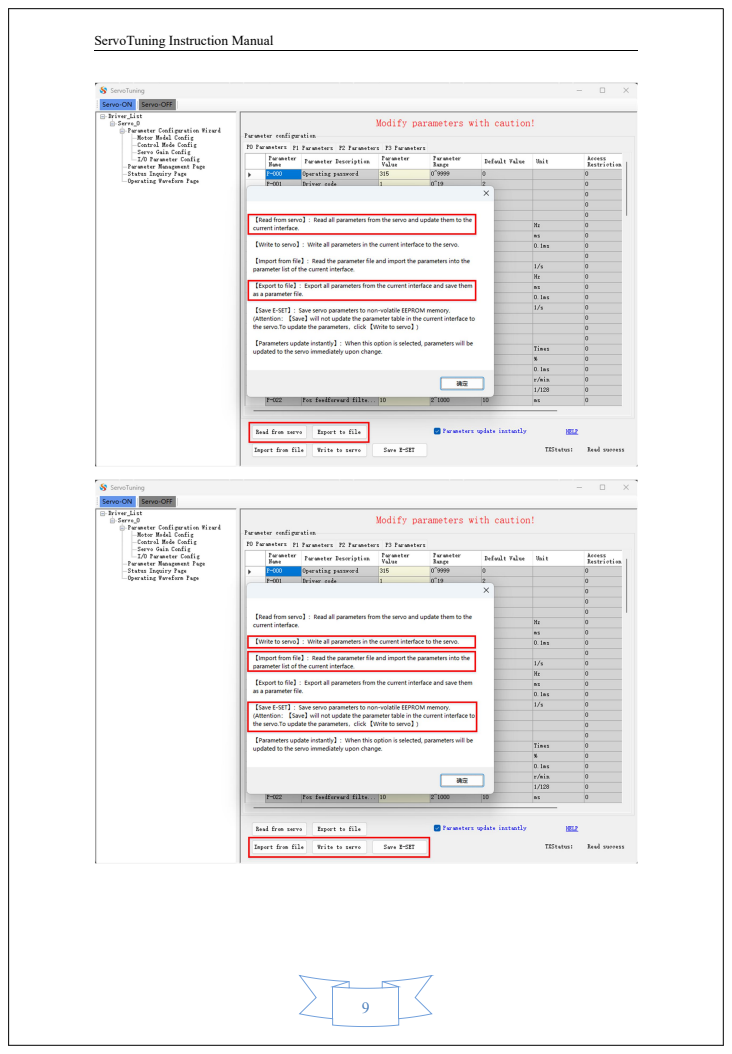
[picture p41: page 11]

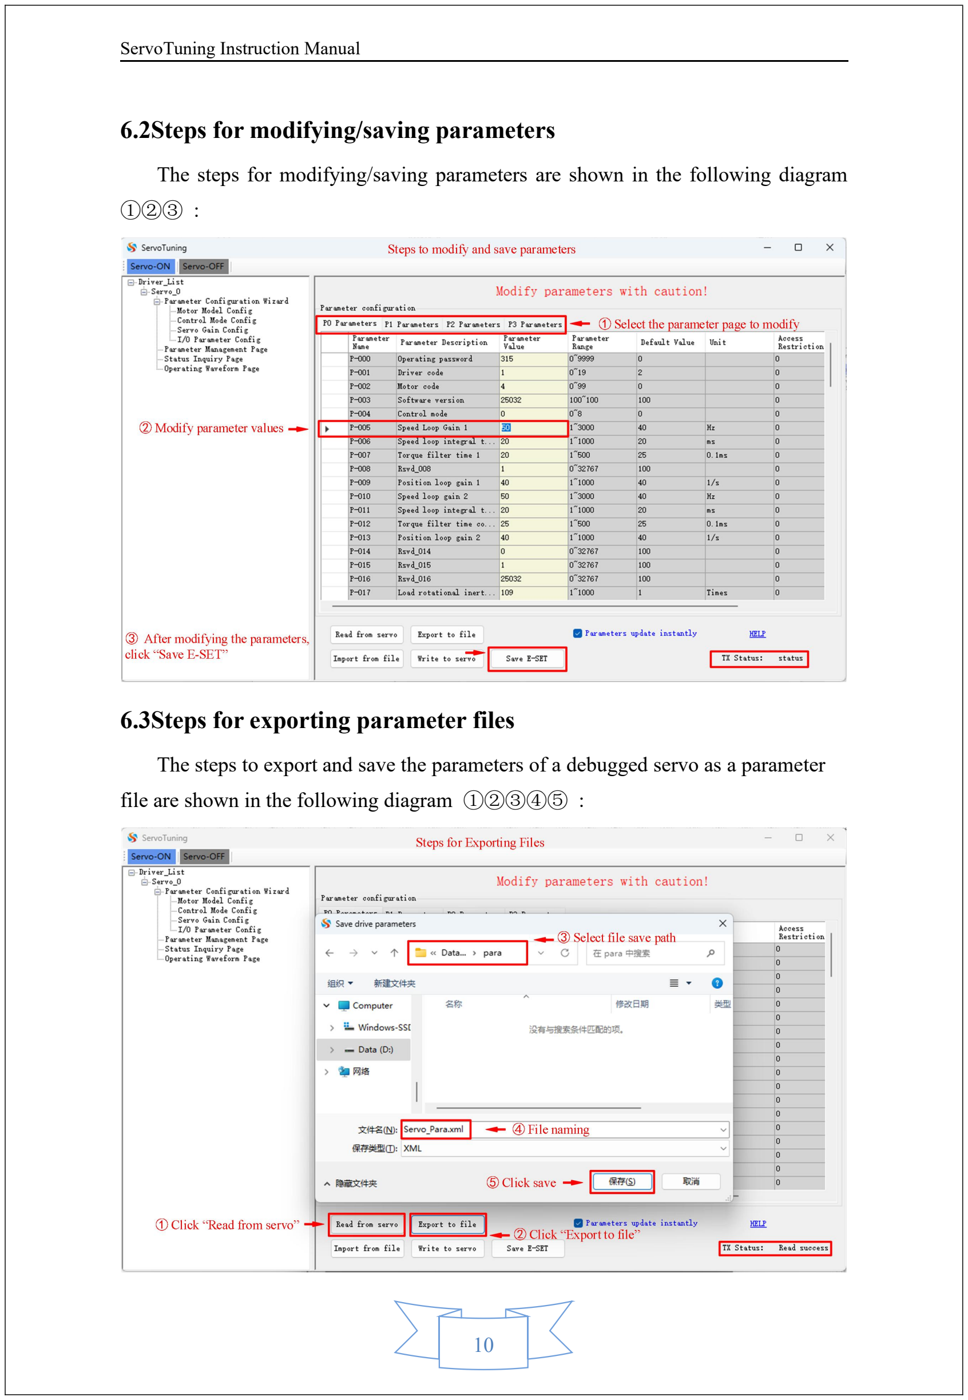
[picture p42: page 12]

### 6.2Steps for modifying/saving parameters

The steps for modifying/saving parameters are shown in the following diagram
①②③ :

### 6.3Steps for exporting parameter files

The steps to export and save the parameters of a debugged servo as a parameter file are shown in the following diagram ①②③④⑤ :

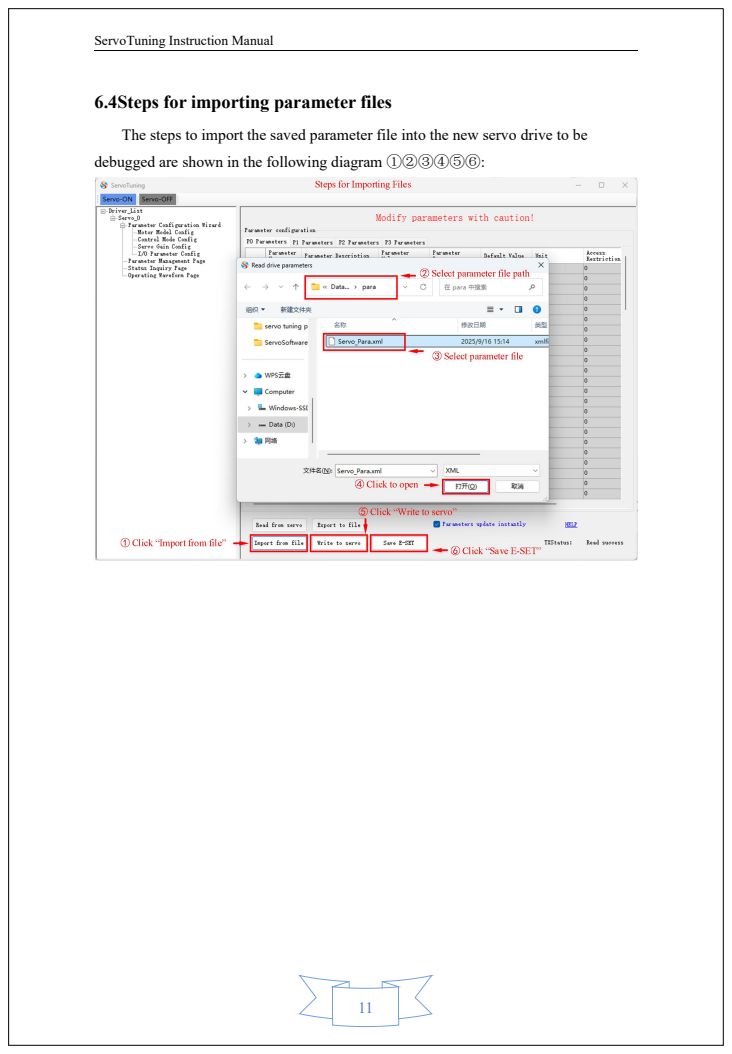
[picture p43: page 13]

6.4Steps for importing parameter files
The steps to import the saved parameter file into the new servo drive to be
debugged are shown in the following diagram ①②③④⑤⑥:

## 7、Status Inquiry Page

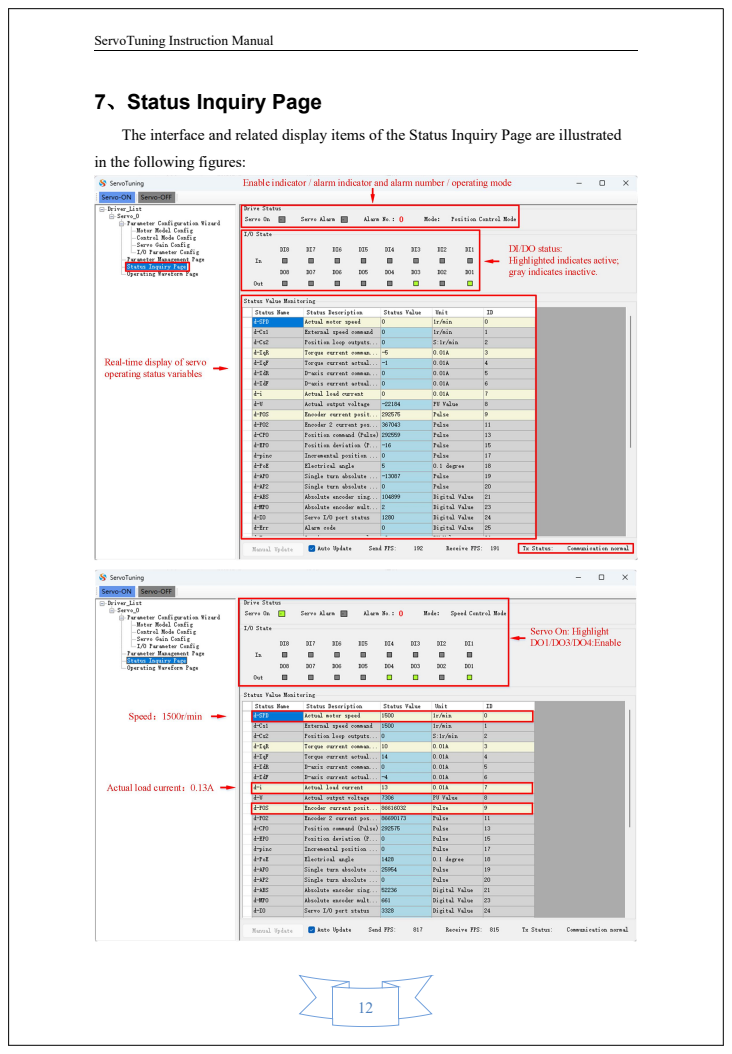
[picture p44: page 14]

The interface and related display items of the Status Inquiry Page are illustrated
in the following figures:

## 8、Operating Waveform Page user guide

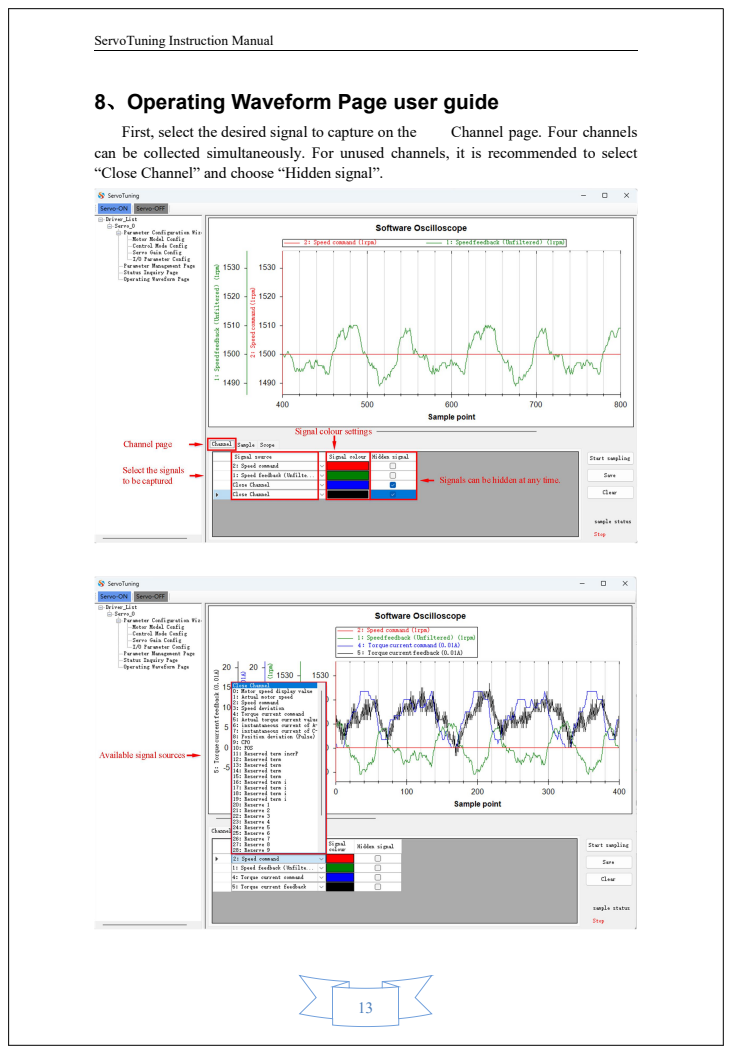
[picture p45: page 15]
First, select the desired signal to capture on the; Channel page. Four channels

can be collected simultaneously. For unused channels, it is recommended to select “Close Channel” and choose “Hidden signal”.

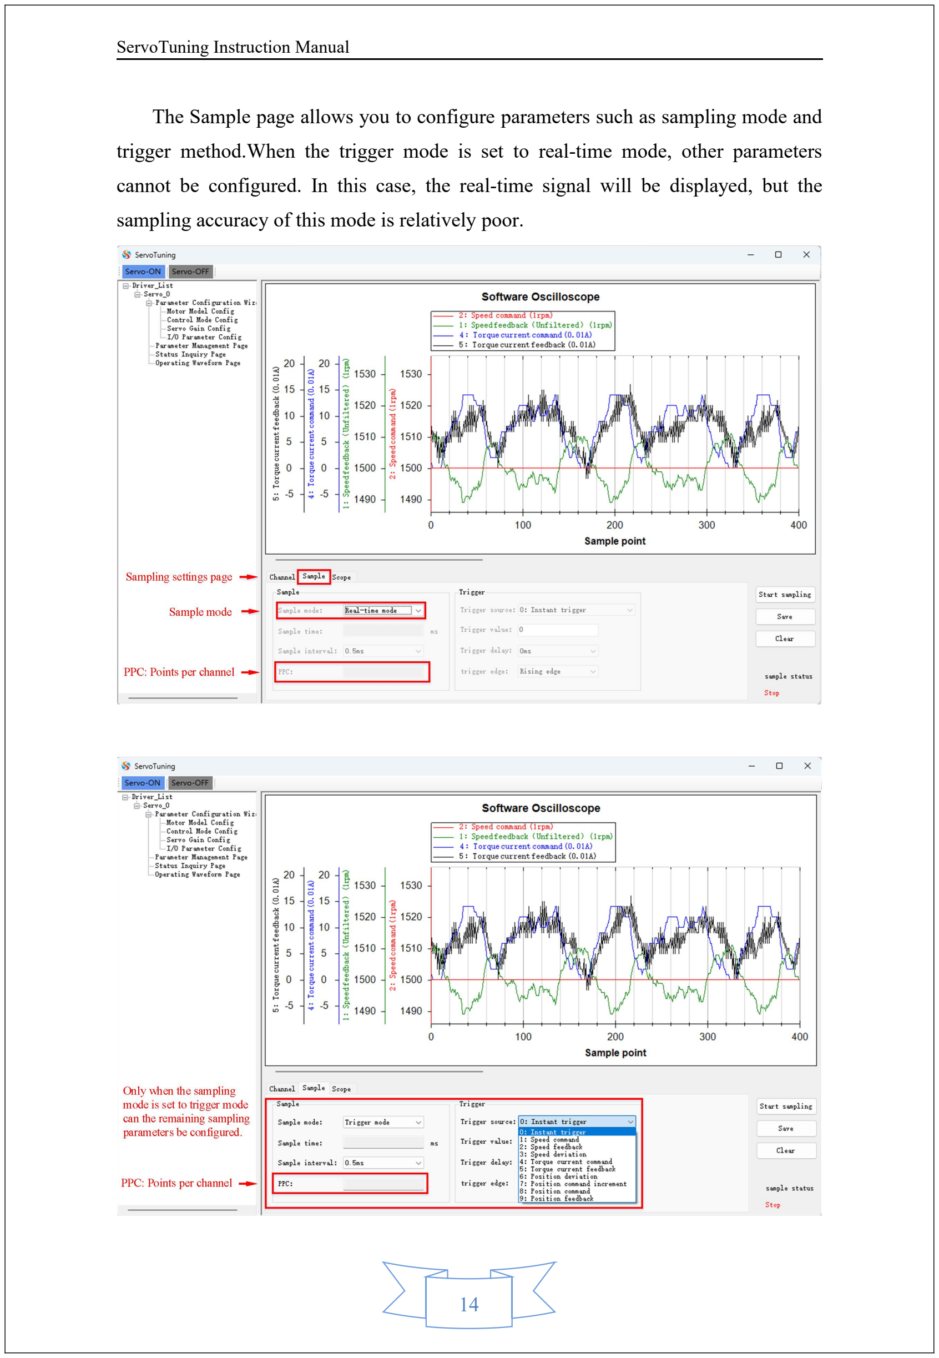
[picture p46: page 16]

The Sample page allows you to configure parameters such as sampling mode and trigger method.When the trigger mode is set to real-time mode, other parameters cannot be configured. In this case, the real-time signal will be displayed, but the sampling accuracy of this mode is relatively poor.

After configuring the signal channel and sampling parameters, click “Start sampling” to capture the signal. Click ‘Save’ to export the waveform to a file, and click “Clear” to erase all waveforms. On the Scope page, the Sample status displays the sampling status in real time. Selecting “Auto-zoom” automatically adjusts the waveform display. You can

configure the oscilloscope's axes to modify the size and position of the displayed waveform.

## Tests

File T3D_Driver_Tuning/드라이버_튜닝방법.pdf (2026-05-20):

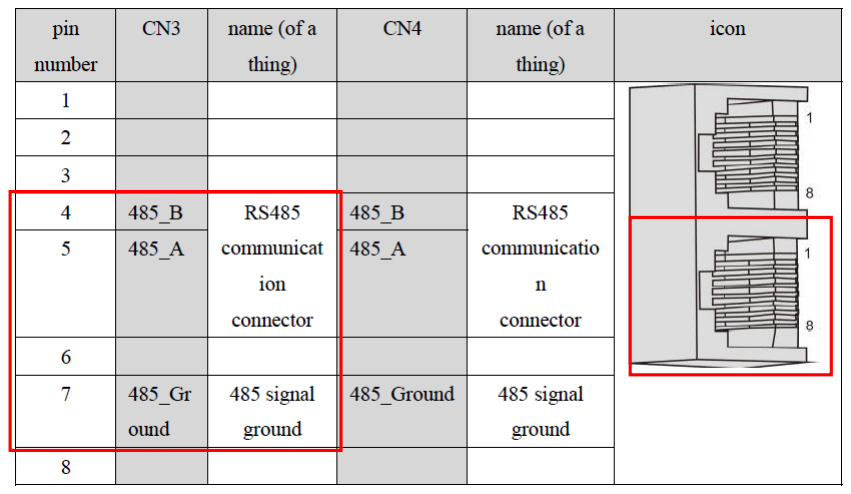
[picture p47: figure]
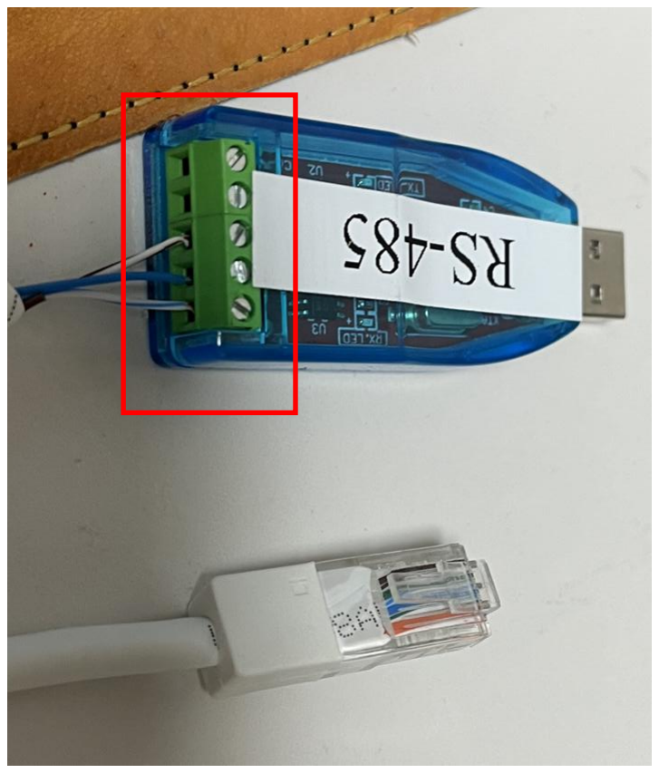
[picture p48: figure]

## 485_A (청/흰) 485_B (청) GND (갈/흰)

## 랜선을 드라이버 디스플레이 가까운쪽에 장착(CN3)

# 1. T3D Driver 통신 Cable 제작

# 2. T3D Driver 연결 방법

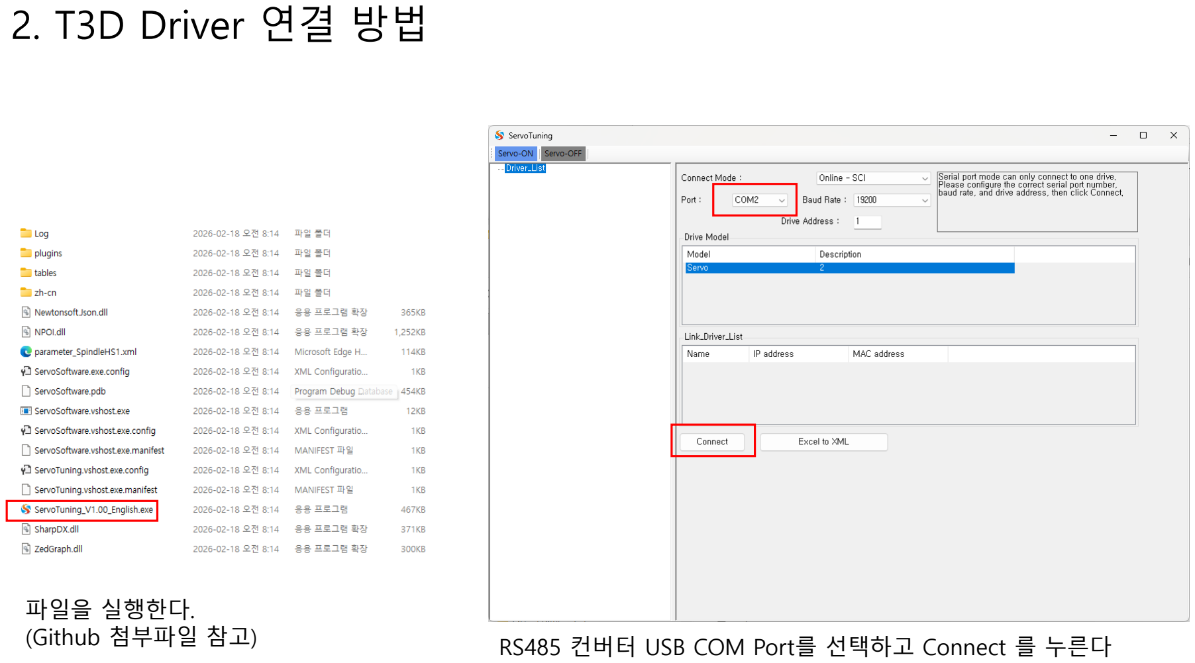
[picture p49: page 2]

## RS485 컨버터 USB COM Port를 선택하고 Connect 를 누른다

파일을 실행한다.

## (Github 첨부파일 참고)

# 3. T3D Driver 게인 튜닝 방법

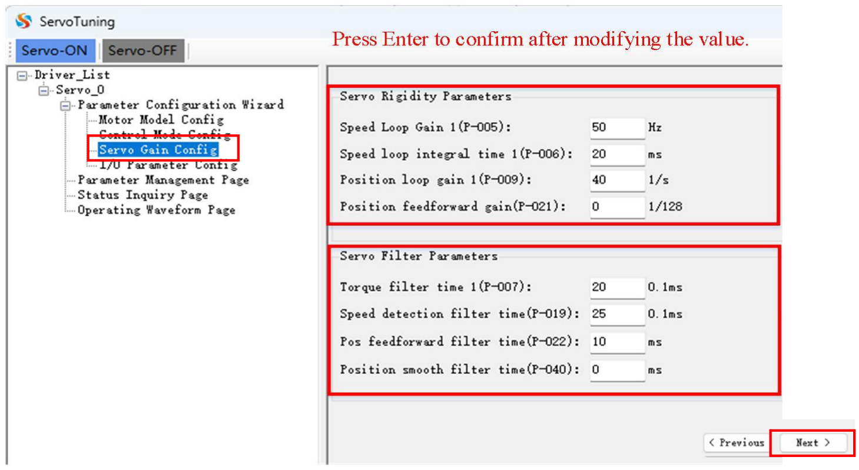
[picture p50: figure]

## Servo Gain Config - Rigidity 와 Filter Prameter 설정

※ 숫자 변경후 입력시 즉시 반영되나,

## Next Page 눌러서 Save E-SET 해줘야 전원 OFF, ON해도

## 변경된값을 유지함

•Speed Loop Gain 1 (P-005)
- 속도 반응 강도 (높을수록 빠르고 딱딱, 진동↑)
- 입력 범위 ( 1 ~ 3000), default : 50

•Speed Loop Integral Time 1 (P-006)
- 속도 오차 누적 보정 속도 (작을수록 빠르게 보정, 불안정↑)
- 입력 범위 ( 1 ~ 1000), default : 20

•Position Loop Gain 1 (P-009)
- 위치 추종 강도 (높을수록 정확/빠름, 진동↑)
- 입력 범위 ( 1 ~ 1000), default : 40

•Position Feedforward Gain (P-021)
- 명령을 미리 따라가는 보정 (높을수록 딜레이 감소, 과하면 튐)
- 입력 범위 ( 0 ~ 100), default : 0

•Torque Filter Time 1 (P-007)
- 토크 신호 부드럽게 (크면 안정, 반응 느림)
- 입력 범위 ( 1 ~ 500), default : 25

•Speed Detection Filter Time (P-019)
- 속도 측정 노이즈 제거 (크면 안정, 반응 느림)
- 입력 범위 ( 5 ~ 500), default : 60

•Pos Feedforward Filter Time (P-022)
- Feedforward 부드럽게 적용 (크면 안정, 효과 감소)
- 입력 범위 ( 2 ~ 1000), default : 10

•Position Smooth Filter Time (P-040)
- 위치 명령 부드럽게 (크면 진동↓, 딜레이↑)
- 입력 범위 ( 0 ~ 5000), default : 0

# 4. T3D Driver Parameter Backup 방법

## 체크 되어있으면 파라미터값 변경시 실시간 적용됨

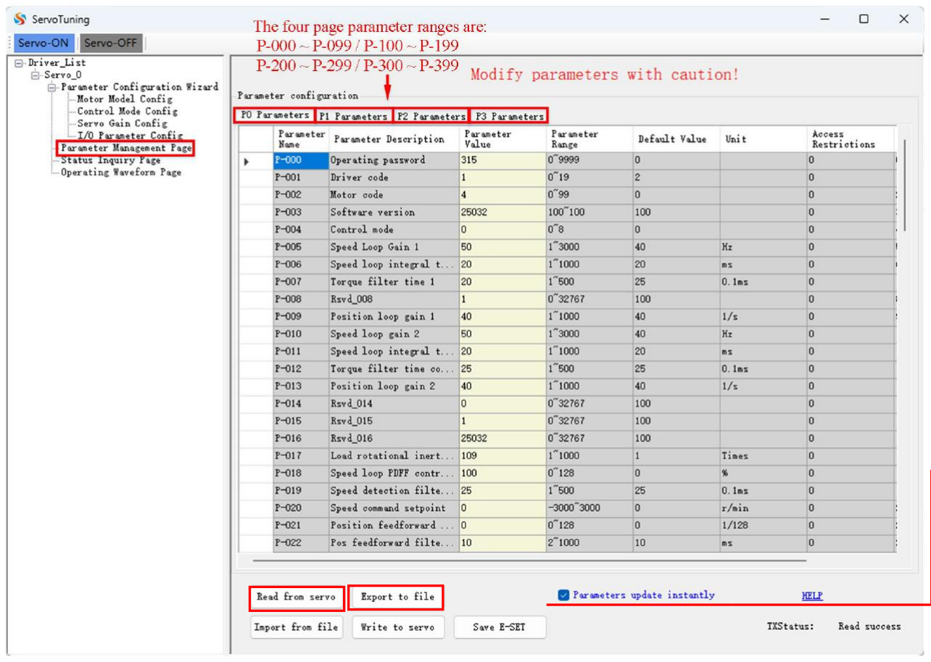
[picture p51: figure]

## 1. Parameter Managemet Page → Read From Servo 눌러서 파라미터 Read

2. Export to File 로 불러온 파일을 저장.

# 5. T3D Driver PC의 저장된 Parameter 복원 방법

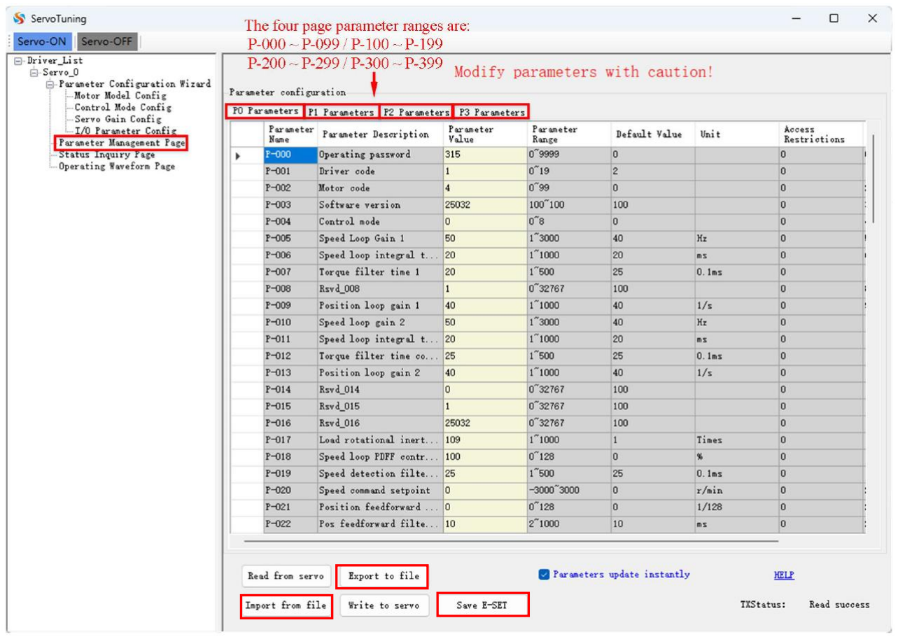
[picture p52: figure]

## 1. Import from File 로 Prameter 파일 불러옴 2. Save E-SET

# 6. 튜닝 방법

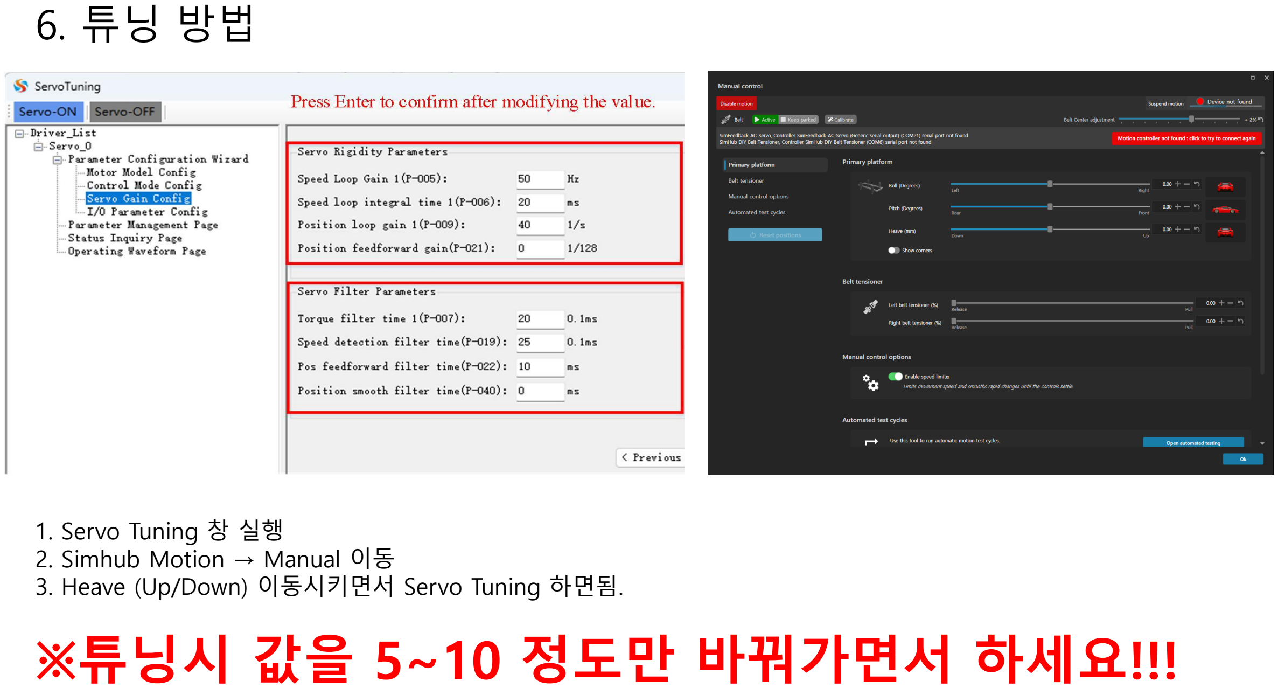
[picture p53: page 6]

## 1. Servo Tuning 창 실행 2. Simhub Motion → Manual 이동

3. Heave (Up/Down) 이동시키면서 Servo Tuning 하면됨.

# ※튜닝시 값을 5~10 정도만 바꿔가면서 하세요!!!

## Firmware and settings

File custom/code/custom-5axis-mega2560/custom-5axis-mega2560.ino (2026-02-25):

// 
// www.lebois-racing.fr/en
// 아두이노 메가(Mega) 전용 - 레지스터 직접 구동 코드
// 5축(5 actuators) 제어를 위한 최적화 버전
// Simhub / FlyPT와 호환

///////////////////////////////////////////////////////////////////
// 80AST-A1C02430
// P-029 = 3 -> 110mm , 6 -> 220mm 
// 중요
///////////////////////////////////////////////////////////////////

// 핀 할당 (직접 포트 조작을 위한 Mega 핀아웃)
// 방향 핀 (DIR)은 PORTA 사용
#define DirPin1   22 // PORTA 비트 0 (PA0)
#define DirPin2   23 // PORTA 비트 1 (PA1)
#define DirPin3   24 // PORTA 비트 2 (PA2)
#define DirPin4   25 // PORTA 비트 3 (PA3)
#define DirPin5   26 // PORTA 비트 4 (PA4)

// 스텝 핀 (STEP)은 PORTC 사용
#define StepPin1  30 // PORTC 비트 7 (PC7)
#define StepPin2  31 // PORTC 비트 6 (PC6)
#define StepPin3  32 // PORTC 비트 5 (PC5)
#define StepPin4  33 // PORTC 비트 4 (PC4)
#define StepPin5  34 // PORTC 비트 3 (PC3)

#define RelayPin  A0 // 릴레이를 통해 파워서플라이(PSU)를 제어합니다.

#define pulseDelay 2      // 액추에이터 속도 설정. 낮을수록 빠릅니다. (2 미만 금지)
#define directionDelay 4

byte buffer           = 0 ;
byte buffercount      = 0 ;
byte commandbuffer[10] = {0}; // 5개 모터 * 2바이트/모터 = 10바이트
unsigned m1Target = 0,   m2Target = 0,   m3Target = 0,   m4Target = 0,   m5Target = 0;
unsigned m1Position = 0, m2Position = 0, m3Position = 0, m4Position = 0, m5Position = 0;
// PORTC의 해당 스텝 비트 위치에 맞게 펄스 값 정의
byte pulseM1 = B10000000, pulseM2 = B01000000, pulseM3 = B00100000, pulseM4 = B00010000, pulseM5 = B00001000;
int  dir1 = -1, dir2 = -1, dir3 = -1, dir4 = -1, dir5 = -1;
byte dirChange = 0;
bool noData = true;
bool servoEnabled = false;

void setup() {
  Serial.begin(921600);    // FlyPT와의 통신 속도

  // 릴레이 핀 설정 및 비활성화
  pinMode(RelayPin, OUTPUT);
  disableServo();

  // 1. 방향 핀(Direction pins) 설정: PORTA (Mega 핀 D22-D26)
  DDRA = DDRA | B00011111;  // PA0-PA4 (비트 0~4)를 OUTPUT으로 설정.
  PORTA |= B00011111;      // PA0-PA4를 HIGH로 설정합니다. (초기 방향)

  // 2. 스텝 핀(Step pins) 설정: PORTC (Mega 핀 D30-D34)
  DDRC = DDRC | B11111000;  // PC3-PC7 (비트 3~7)을 OUTPUT으로 설정합니다.
}

void loop() {
  SerialReader();
  moveMotor();
}

void SerialReader() {       
  while (Serial.available())
  {
    if (buffercount == 0)
    {
      buffer = Serial.read();
      if (buffer != 'T') { 
        if(buffer =='A'){enableServo();}
        if(buffer =='C'){disableServo();}     
                      
        buffercount = 0;
      } else {
        buffercount = 1;
      }
    }
    else
    {
      buffer = Serial.read();
      commandbuffer[buffercount-1] = buffer; 
      buffercount++;
      if (buffercount >= 11) { // 1 마커 + 5 모터 * 2바이트/모터 = 총 11바이트
          m1Target = ((uint16_t)commandbuffer[0] << 8) | commandbuffer[1];
          m2Target = ((uint16_t)commandbuffer[2] << 8) | commandbuffer[3];
          m3Target = ((uint16_t)commandbuffer[4] << 8) | commandbuffer[5];
          m4Target = ((uint16_t)commandbuffer[6] << 8) | commandbuffer[7];
          m5Target = ((uint16_t)commandbuffer[8] << 8) | commandbuffer[9];
          buffercount = 0;
        break;
      }
    }
  }
}

void moveMotor() {
  directionManager(); 
  singleStep();
}

void directionManager() { 
// PORTA는 DirPin1 (PA0)부터 DirPin5 (PA4)까지 제어합니다.

  // M1 (PA0 - Bit 0)
  if ((m1Target > m1Position) && (dir1 == -1)) {
    PORTA &= B11111110; // PA0를 LOW로 설정
    dir1 = 1;
    dirChange = 1;
  }
  if ((m1Target < m1Position ) && (dir1 == 1)) {
    PORTA |= B00000001; // PA0를 HIGH로 설정
    dir1 = -1;
    dirChange = 1;
  }

  // M2 (PA1 - Bit 1)
  if ((m2Target > m2Position) && (dir2 == -1)) {
    PORTA &= B11111101; // PA1를 LOW로 설정
    dir2 = 1;
    dirChange = 1;
  }
  if ((m2Target < m2Position ) && (dir2 == 1)) {
    PORTA |= B00000010; // PA1를 HIGH로 설정
    dir2 = -1;
    dirChange = 1;
  }

  // M3 (PA2 - Bit 2)
  if ((m3Target > m3Position) && (dir3 == -1)) {
    PORTA &= B11111011; // PA2를 LOW로 설정
    dir3 = 1;
    dirChange = 1;
  }
  if ((m3Target < m3Position ) && (dir3 == 1)) {
    PORTA |= B00000100; // PA2를 HIGH로 설정
    dir3 = -1;
    dirChange = 1;
  }

  // M4 (PA3 - Bit 3)
  if ((m4Target > m4Position) && (dir4 == -1)) {
    PORTA &= B11110111; // PA3를 LOW로 설정
    dir4 = 1;
    dirChange = 1;
  }
  if ((m4Target < m4Position ) && (dir4 == 1)) {
    PORTA |= B00001000; // PA3를 HIGH로 설정
    dir4 = -1;
    dirChange = 1;
  }
  
  // M5 (PA4 - Bit 4)
  if ((m5Target > m5Position) && (dir5 == -1)) {
    PORTA &= B11101111; // PA4를 LOW로 설정
    dir5 = 1;
    dirChange = 1;
  }
  if ((m5Target < m5Position ) && (dir5 == 1)) {
    PORTA |= B00010000; // PA4를 HIGH로 설정
    dir5 = -1;
    dirChange = 1;
  }
  
  if (dirChange == 1) {
    delayMicroseconds(directionDelay);
    dirChange = 0;
  }
}

void singleStep() {
  // 펄스는 StepPin1 (PC7)부터 StepPin5 (PC3)까지입니다.
  byte activePulses = 0;
  
  if (m1Target != m1Position) {
    activePulses |= pulseM1; // PC7
    m1Position += dir1;
  }
  
  if (m2Target != m2Position) {
    activePulses |= pulseM2; // PC6
    m2Position += dir2;
  }
    
  if (m3Target != m3Position) {
    activePulses |= pulseM3; // PC5
    m3Position += dir3;
  }

  if (m4Target != m4Position) {
    activePulses |= pulseM4; // PC4
    m4Position += dir4;
  }
  
  if (m5Target != m5Position) {
    activePulses |= pulseM5; // PC3
    m5Position += dir5;
  }
    
  if(activePulses == 0){return;}

  // 1. HIGH 펄스를 발생시킵니다. (5개 펄스 동시 발생)
  PORTC |= activePulses; 
  delayMicroseconds(pulseDelay);

  // 2. 펄스를 CLEAR (LOW) 합니다. (5개 펄스 동시 초기화)
  PORTC &= B00000111; 
}

void enableServo(){
    digitalWrite(RelayPin, LOW);
    servoEnabled=true;
}
void disableServo(){
    digitalWrite(RelayPin, HIGH);
    servoEnabled=false;
}

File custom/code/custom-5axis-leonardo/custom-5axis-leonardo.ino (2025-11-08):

#define StepPin1  8
#define StepPin2  9
#define StepPin3  10
#define StepPin4  11
#define StepPin5  12

#define DirPin1   4
#define DirPin2   5
#define DirPin3   6
#define DirPin4   7
#define DirPin5   3

#define RelayPin  A0

#define pulseDelay 2
#define directionDelay 4

byte buffer = 0;
byte buffercount = 0;
byte commandbuffer[10] = {0};

unsigned m1Target = 0, m2Target = 0, m3Target = 0, m4Target = 0, m5Target = 0;
unsigned m1Position = 0, m2Position = 0, m3Position = 0, m4Position = 0, m5Position = 0;

int dir1 = -1, dir2 = -1, dir3 = -1, dir4 = -1, dir5 = -1;
byte dirChange = 0;
bool servoEnabled = false;

void setup() {
  Serial.begin(921600);

  pinMode(RelayPin, OUTPUT);
  disableServo();

  pinMode(StepPin1, OUTPUT);
  pinMode(StepPin2, OUTPUT);
  pinMode(StepPin3, OUTPUT);
  pinMode(StepPin4, OUTPUT);
  pinMode(StepPin5, OUTPUT);

  pinMode(DirPin1, OUTPUT);
  pinMode(DirPin2, OUTPUT);
  pinMode(DirPin3, OUTPUT);
  pinMode(DirPin4, OUTPUT);
  pinMode(DirPin5, OUTPUT);

  digitalWrite(DirPin1, HIGH);
  digitalWrite(DirPin2, HIGH);
  digitalWrite(DirPin3, HIGH);
  digitalWrite(DirPin4, HIGH);
  digitalWrite(DirPin5, HIGH);
}

void loop() {
  SerialReader();
  moveMotor();
}

void SerialReader() {
  while (Serial.available()) {
    if (buffercount == 0) {
      buffer = Serial.read();
      if (buffer != 'T') {
        if (buffer == 'A') { enableServo(); }
        if (buffer == 'C') { disableServo(); }
        buffercount = 0;
      } else {
        buffercount = 1;
      }
    } else {
      buffer = Serial.read();
      commandbuffer[buffercount - 1] = buffer;
      buffercount++;
      if (buffercount >= 11) {
        m1Target = commandbuffer[0] * 256 + commandbuffer[1];
        m2Target = commandbuffer[2] * 256 + commandbuffer[3];
        m3Target = commandbuffer[4] * 256 + commandbuffer[5];
        m4Target = commandbuffer[6] * 256 + commandbuffer[7];
        m5Target = commandbuffer[8] * 256 + commandbuffer[9];
        buffercount = 0;
        break;
      }
    }
  }
}

void moveMotor() {
  directionManager();
  singleStep();
}

void directionManager() {
  if ((m1Target > m1Position) && (dir1 == -1)) {
    PORTD &= ~(1 << 4);
    dir1 = 1;
    dirChange = 1;
  }
  if ((m1Target < m1Position) && (dir1 == 1)) {
    PORTD |= (1 << 4);
    dir1 = -1;
    dirChange = 1;
  }

  if ((m2Target > m2Position) && (dir2 == -1)) {
    PORTC &= ~(1 << 6);
    dir2 = 1;
    dirChange = 1;
  }
  if ((m2Target < m2Position) && (dir2 == 1)) {
    PORTC |= (1 << 6);
    dir2 = -1;
    dirChange = 1;
  }

  if ((m3Target > m3Position) && (dir3 == -1)) {
    PORTD &= ~(1 << 7);
    dir3 = 1;
    dirChange = 1;
  }
  if ((m3Target < m3Position) && (dir3 == 1)) {
    PORTD |= (1 << 7);
    dir3 = -1;
    dirChange = 1;
  }

  if ((m4Target > m4Position) && (dir4 == -1)) {
    PORTE &= ~(1 << 6);
    dir4 = 1;
    dirChange = 1;
  }
  if ((m4Target < m4Position) && (dir4 == 1)) {
    PORTE |= (1 << 6);
    dir4 = -1;
    dirChange = 1;
  }

  if ((m5Target > m5Position) && (dir5 == -1)) {
    PORTD &= ~(1 << 0);
    dir5 = 1;
    dirChange = 1;
  }
  if ((m5Target < m5Position) && (dir5 == 1)) {
    PORTD |= (1 << 0);
    dir5 = -1;
    dirChange = 1;
  }

  if (dirChange == 1) {
    delayMicroseconds(directionDelay);
    dirChange = 0;
  }
}

void singleStep() {
  byte portbPulse = 0;
  byte portdPulse = 0;

  if (m1Target != m1Position) {
    portbPulse |= (1 << 4);
    m1Position += dir1;
  }
  if (m2Target != m2Position) {
    portbPulse |= (1 << 5);
    m2Position += dir2;
  }
  if (m3Target != m3Position) {
    portbPulse |= (1 << 6);
    m3Position += dir3;
  }
  if (m4Target != m4Position) {
    portbPulse |= (1 << 7);
    m4Position += dir4;
  }
  if (m5Target != m5Position) {
    portdPulse |= (1 << 6);
    m5Position += dir5;
  }

  if (portbPulse == 0 && portdPulse == 0) return;

  if (portbPulse) PORTB |= portbPulse;
  if (portdPulse) PORTD |= portdPulse;

  delayMicroseconds(pulseDelay);

  if (portbPulse) PORTB &= ~(0xF0);
  if (portdPulse) PORTD &= ~(1 << 6);
}

void enableServo() {
  digitalWrite(RelayPin, LOW);
  servoEnabled = true;
}

void disableServo() {
  digitalWrite(RelayPin, HIGH);
  servoEnabled = false;
}

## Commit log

2025-09-04 모델링 파일 추가
    inventor로 모델링
    [100100W-PROFILE.ipt, 80AST-A1C02430.ipt, BALL_NUT.ipt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]
2025-09-04 참고링크 추가
2025-09-06 3D Models update - created by Fusion
    [100100W-PROFILE.ipt, 80AST-A1C02430.ipt, BALL_NUT.ipt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]
2025-09-08 update model
    [SFX-100.f3z]
2025-09-29 fusion model update
    [SFX-100.f3z]
2026-03-22 Create Tuning 프로그램 비밀번호 는 없습니다.
2026-05-17 Add Tuning_프로그램_비밀번호는_없습니다 file
    rename
2026-05-17 Rename Tuning_프로그램_비밀번호는_없습니다. to Tuning_프로그램_비밀번호는_없습니다.txt
    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
2026-05-17 파일이름정리
    [에어스프링_어댑터2.f3d, 에어스프링_어댑터2.stl]
